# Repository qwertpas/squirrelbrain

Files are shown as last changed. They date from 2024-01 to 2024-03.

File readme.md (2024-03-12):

## Squirrelbrain v2

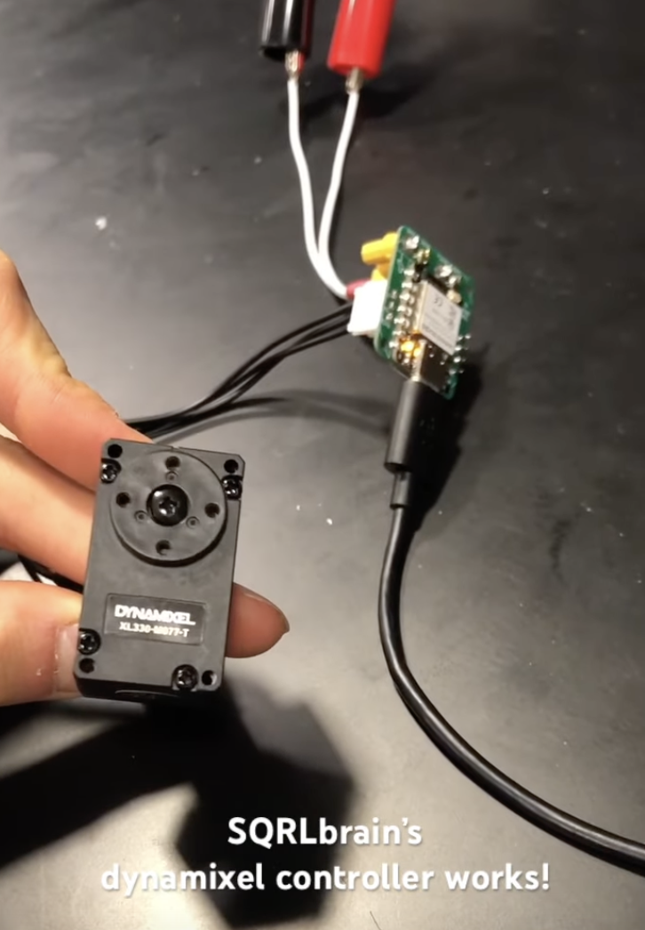
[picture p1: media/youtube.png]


[Youtube video](https://youtube.com/shorts/pgTb6q6fkRE?feature=shared)

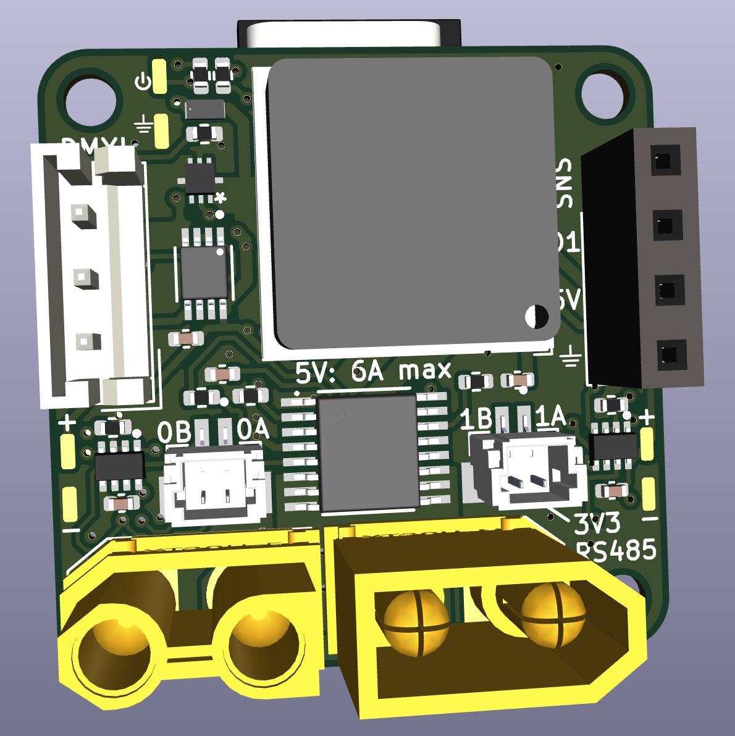
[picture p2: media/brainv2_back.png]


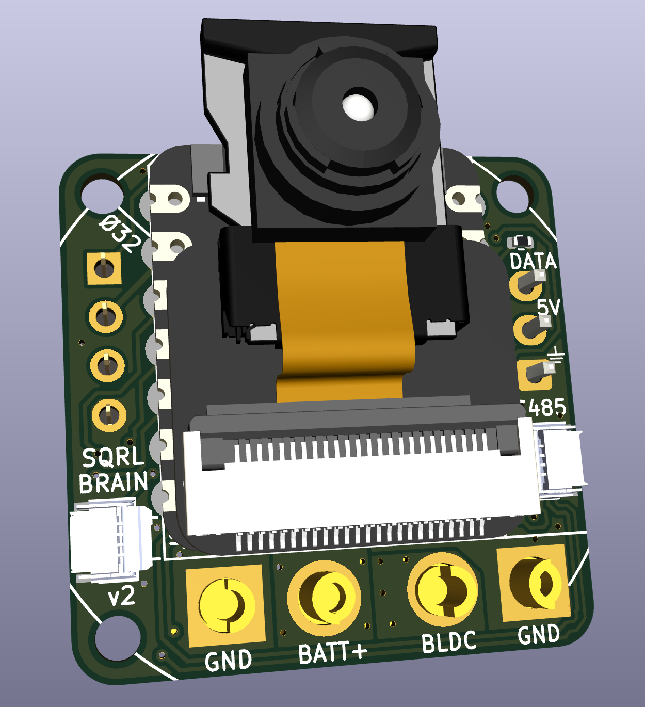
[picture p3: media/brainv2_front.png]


Main control board for the [Pintobotics](https://pintobotics.substack.com) robotic squirrel. It uses a Seeeduino XIAO ESP32S3 for wireless communication with a base station, is able to drive [dynamixel 5V TTL servos](https://www.robotis.us/dynamixel-xl330-m077-t/) up to 6A, and has two separate RS485 buses. 

The RS485 buses are intended for:
* [Ø32controller](https://github.com/qwertpas/O32controller), a miniature closed-loop brushless motor driver
* [Ø12encoder](https://github.com/qwertpas/O12encoder), a miniature magnetic encoder (MA702)
* [Ø12imu](https://github.com/qwertpas/O12imu), a miniature IMU with built-in sensor fusion for orientation (LSM6DSV) 

Squirrelbrain has two load switches to allow the ESP32 to cut off power to the motors when the battery is still connected. One load switch operates an XT30 output, featuring current sensing and a programmed current limit of 38A (limit can be adjusted by replacing a resistor). The other load switch operates on the 5V supply intended for dynamixel servos.

Size: 27mm x 27mm

Mounting: 4x M2 on 32mm diameter circle 

Connections:
* 2x JST-SH 2pin connectors for RS485 communication (1 for each bus)
* 2x 4pin 0.5mm pitch double-sided FFC connectors for RS485 communication (1 for each bus)
* 2x solder pads for 3.3V output
* JST-EH 3pin connector for dynamixel TTL
* USB-C on the ESP32S3
* Optional camera module on the ESP32S3
* XT30U-M power in (5-15V)
* XT30U-F power out
* 4pin header for current sense output, extra GPIO, and 5V/GND output

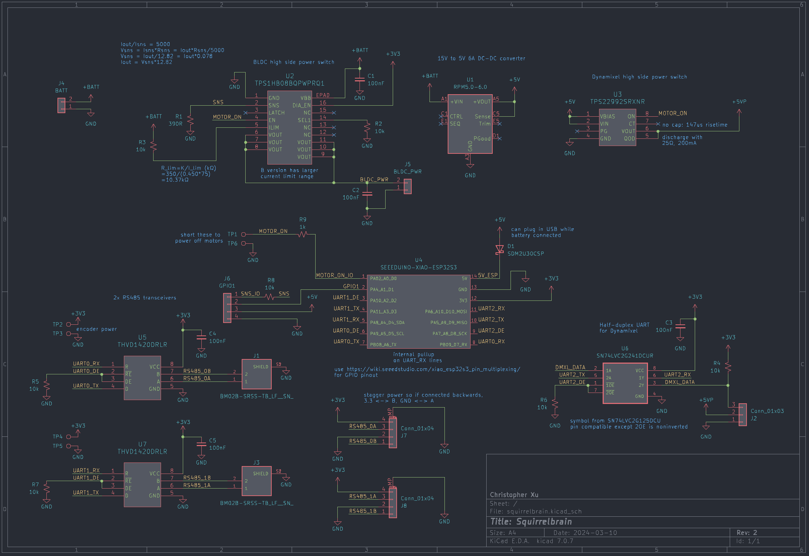
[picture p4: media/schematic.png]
Schematic


#### Changelog from Squirrelbrain v1:
Squirrelbrain v1 does not have the FFC connectors and is missing a pullup on the dynamixel data line.

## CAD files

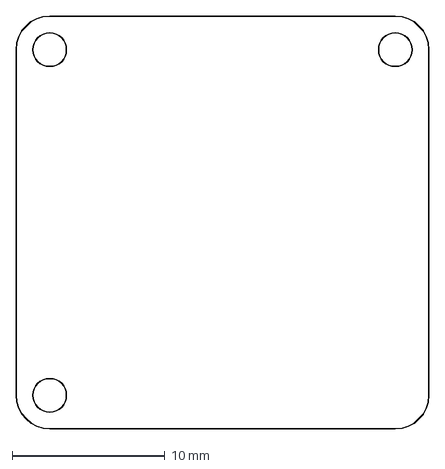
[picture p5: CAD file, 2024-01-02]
v2/dxf/O32.dxf
27.0 x 27.0 mm

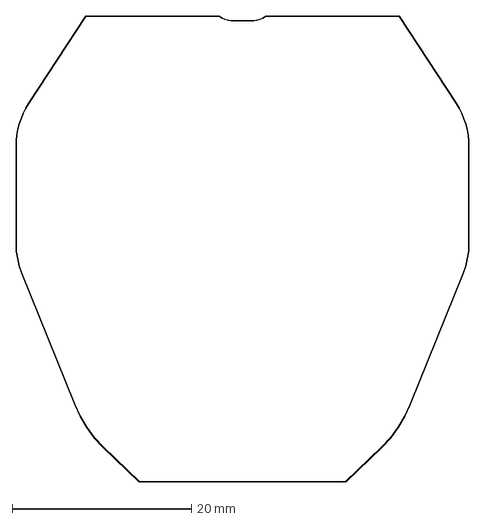
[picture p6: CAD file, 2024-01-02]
v2/dxf/oldbraincase.dxf
50.5 x 52.0 mm

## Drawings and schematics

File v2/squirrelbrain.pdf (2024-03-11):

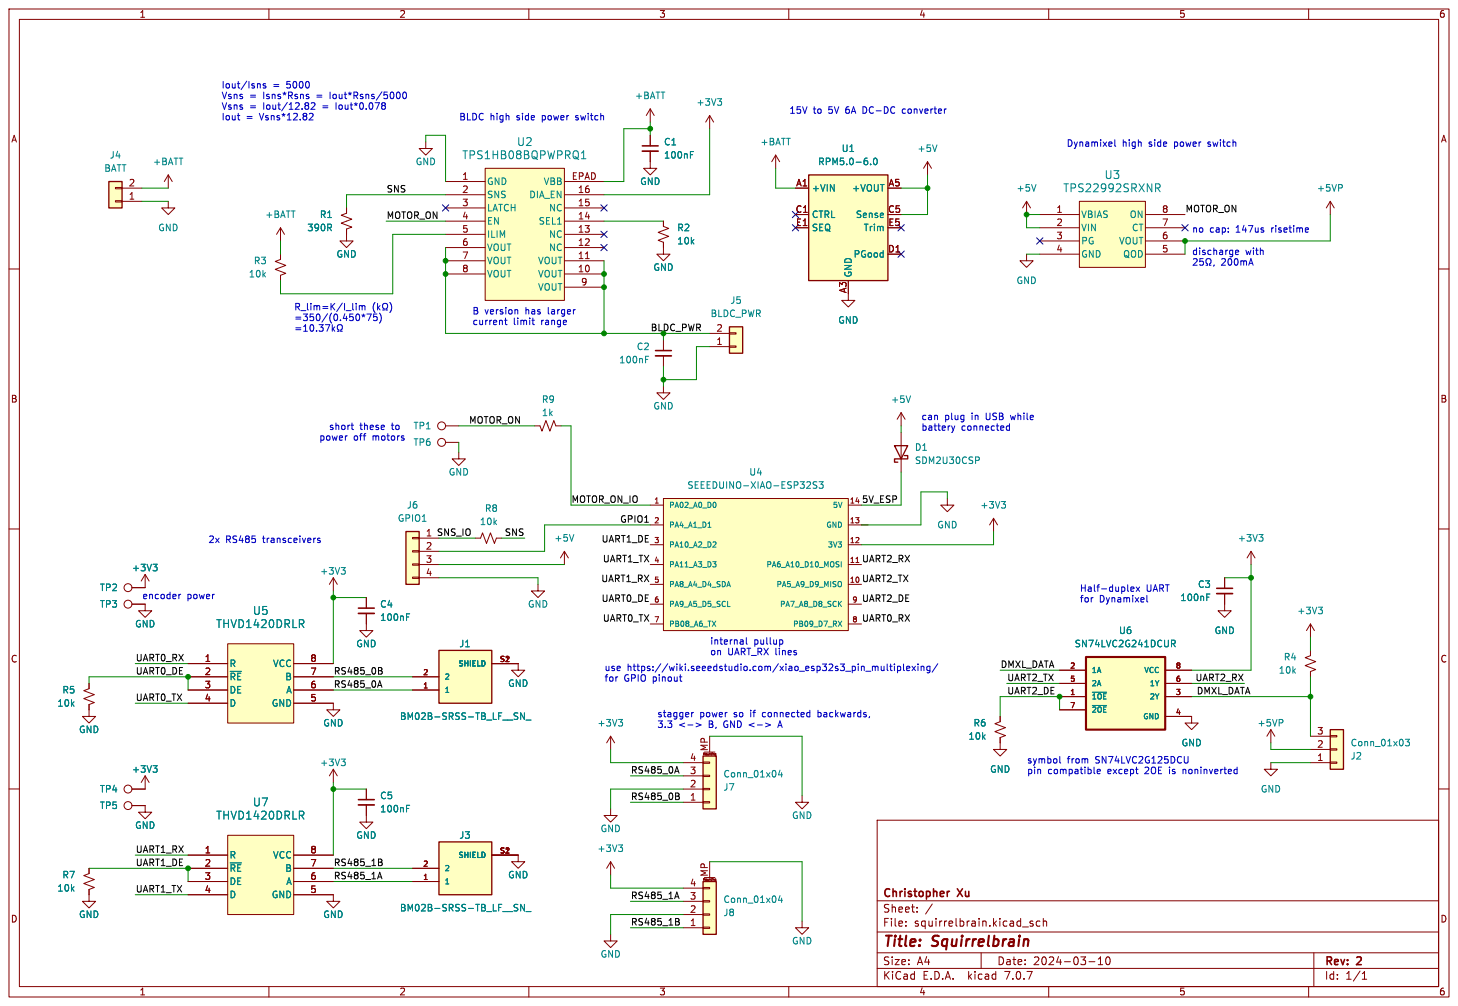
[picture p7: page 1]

15V to 5V 6A DC-DC converter

B version has larger current limit range

can plug in USB while

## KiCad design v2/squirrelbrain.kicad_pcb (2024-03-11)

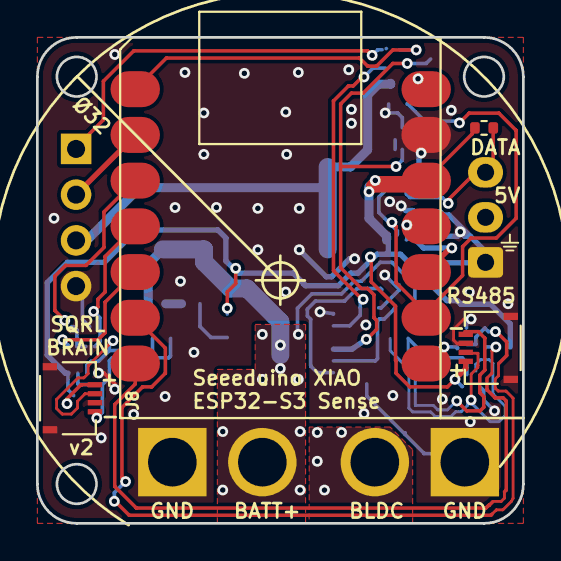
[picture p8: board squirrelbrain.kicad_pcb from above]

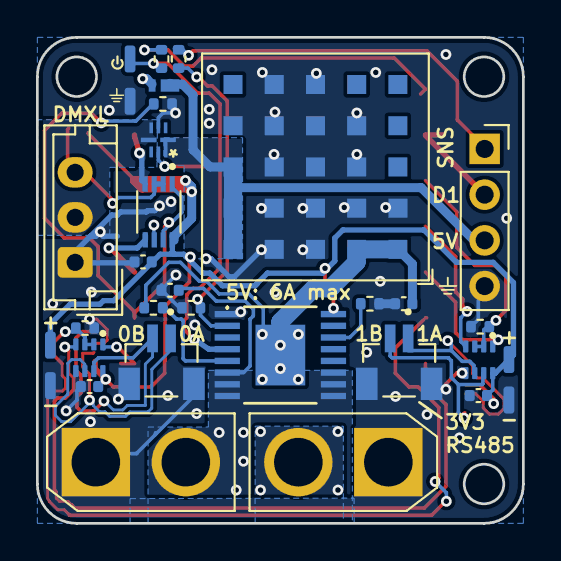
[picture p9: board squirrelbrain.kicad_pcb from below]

Board: 2 copper layers, 27.0 x 27.0 mm, 36 parts (32 on the bottom side), 28 nets.

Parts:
C1, C2, C3, C4, C5: 100nF; C_0402_1005Metric
D1: SDM2U30CSP; SDM2U30CSP-7
J1, J3: BM02B-SRSS-TB_LF__SN_; JST_BM02B-SRSS-TB_LF__SN_
J2: Conn_01x03; JST_EH_B3B-EH-A_1x03_P2.50mm_Vertical
J4: BATT; AMASS_XT30U-M_1x02_P5.0mm_Vertical
J5: BLDC_PWR; AMASS_XT30U-F_1x02_P5.0mm_Vertical
J6: GPIO1; PinSocket_1x04_P2.54mm_Vertical
J7, J8: Conn_01x04; TE_2328702-4
R1: 390R; R_0402_1005Metric
R2, R3, R4, R5, R6, R7, R8: 10k; R_0402_1005Metric
R9: 1k; R_0402_1005Metric
TP1, TP2, TP3, TP4, TP5, TP6: TestPoint; TestPoint_Pad_Rect
U1: RPM5.0-6.0; Converter_DCDC_RECOM_RPMx.x-x.0
U2: TPS1HB08BQPWPRQ1; TPS1HB08
U3: TPS22992SRXNR; TPS22992S
U4: SEEEDUINO-XIAO-ESP32S3; XIAO-ESP32S3-2.54-21X17.8MM
U5, U7: THVD1420DRLR; THVD1420DRLR_SOT-585
U6: SN74LVC2G241DCUR; SN74LVC2G125DCU

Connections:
+3V3: C3.1, C4.1, C5.1, J7.4, J8.4, R4.2, TP2.1, TP4.1, U2.16 (DIA_EN), U4.12 (3V3), U5.8 (VCC), U6.8 (VCC), U7.8 (VCC)
+5V: D1.2 (A), J6.3, U1.A5 (+VOUT), U1.B5 (+VOUT), U1.C5 (Sense), U3.1 (VBIAS), U3.2 (VIN)
+5VP: J2.2, U3.5 (QOD), U3.6 (VOUT)
+BATT: C1.1, J4.2, R3.2, U1.A1 (+VIN), U1.A2 (+VIN), U2.EPAD (VBB)
/5V_ESP: D1.1 (K), U4.14 (5V)
/BLDC_PWR: C2.1, J5.2, U2.6 (VOUT), U2.7 (VOUT), U2.8 (VOUT), U2.9 (VOUT), U2.10 (VOUT), U2.11 (VOUT)
/DMXL_DATA: J2.3, R4.1, U6.2 (1A), U6.3 (2Y)
/GPIO1: J6.2, U4.2 (PA4_A1_D1)
/MOTOR_ON: R9.1, TP1.1, U2.4 (EN), U3.8 (ON)
/MOTOR_ON_IO: R9.2, U4.1 (PA02_A0_D0)
/RS485_0A: J1.1, J7.3, U5.6 (A)
/RS485_0B: J1.2, J7.1, U5.7 (B)
/RS485_1A: J3.1, J8.3, U7.6 (A)
/RS485_1B: J3.2, J8.1, U7.7 (B)
/SNS: R1.2, R8.1, U2.2 (SNS)
/SNS_IO: J6.1, R8.2
/UART0_DE: R5.2, U4.6 (PA9_A5_D5_SCL), U5.2 (~RE), U5.3 (DE)
/UART0_RX: U4.8 (PB09_D7_RX), U5.1 (R)
/UART0_TX: U4.7 (PB08_A6_TX), U5.4 (D)
/UART1_DE: R7.2, U4.3 (PA10_A2_D2), U7.2 (~RE), U7.3 (DE)
/UART1_RX: U4.5 (PA8_A4_D4_SDA), U7.1 (R)
/UART1_TX: U4.4 (PA11_A3_D3), U7.4 (D)
/UART2_DE: R6.2, U4.9 (PA7_A8_D8_SCK), U6.1 (~1OE), U6.7 (~2OE)
/UART2_RX: U4.11 (PA6_A10_D10_MOSI), U6.6 (1Y)
/UART2_TX: U4.10 (PA5_A9_D9_MISO), U6.5 (2A)
GND: C1.2, C2.2, C3.2, C4.2, C5.2, J1.S1 (SHIELD), J1.S2 (SHIELD), J2.1, J3.S1 (SHIELD), J3.S2 (SHIELD), J4.1, J5.1, J6.4, J7.2, J7.MP (MountPin), J8.2, J8.MP (MountPin), R1.1, R2.1, R5.1, R6.1, R7.1, TP3.1, TP5.1, TP6.1, U1.A3 (GND), U1.A4 (GND), U1.B1 (GND), U1.B2 (GND), U1.B3 (GND), U1.B4 (GND), U1.C2 (GND), U1.C3 (GND), U1.C4 (GND), U1.D2 (GND), U1.D3 (GND), U1.D4 (GND), U1.D5 (GND), U1.E3 (GND), U1.E4 (GND), U2.1 (GND), U3.4 (GND), U4.13 (GND), U5.5 (GND), U6.4 (GND), U7.5 (GND)
unnamed: R3.1, U2.5 (ILIM)
unnamed: R2.2, U2.14 (SEL1)

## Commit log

2024-01-02 first commit, pick parts and pin mapping
    [oldbraincase.dxf, squirrelbrain.kicad_pcb, squirrelbrain.kicad_sch]
2024-01-02 chose high side load switches
    [squirrelbrain.kicad_pcb, squirrelbrain.kicad_sch]
2024-01-02 add xt30, start routing
    [O32.dxf, squirrelbrain.kicad_pcb, squirrelbrain.kicad_sch]
2024-01-02 finished routing? need to add 3v3 breakout
    [squirrelbrain.kicad_pcb, squirrelbrain.kicad_sch]
2024-01-03 rect test pads for 3v3
    [squirrelbrain.kicad_pcb, squirrelbrain.kicad_sch]
2024-01-03 generate gerbers
    [squirrelbrain-B_Cu.gbl, squirrelbrain-B_Mask.gbs, squirrelbrain-B_Paste.gbp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]
2024-02-13 add schematic labels just for reference
    [squirrelbrain.kicad_pcb, squirrelbrain.kicad_sch]
2024-03-11 readme, export pdf
    [O32.dxf, oldbraincase.dxf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]
2024-03-12 youtube video frame and smaller pics
